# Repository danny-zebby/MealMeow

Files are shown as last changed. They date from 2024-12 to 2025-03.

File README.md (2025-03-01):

# MealMeow

## General Description
The general concept of this design seeks to solve the problem of caring for your cats or dogs while you are away for an extended period of time. Our aim is to create a product that can handle the feeding and hydrating of several pets while the owner is away. We will create a device that will dispense water, and food to pets at amounts configurable by the owner at regular intervals and it will do so independently. Our product will only require the attention of the owner when any of the aforementioned items is depleted. When food has run low, or when any of the dispensable items have run out, our device will alert the owner using sound alerts and a warning indicator light.

## Behavioral Specification
### Food Storage and Dispensation
Food will be stored in a container and will be dispensed using a rotating paddle at the bottom of the container. We intend to control this rotating paddle using a direct-current stepper motor. The food container will be equipped with a IR distance sensor placed at one side of the container, once the IR distance sensor measures the other side of the container, it will be known that there is no food at that level. This will cause the unit to light an LED as a low food level indicator for the user. As an alternative, another sensor can be reading the distance between the sensor and what’s in front. 
Once the food level sensor measures that the container is low on food, our product will notify the user of low food levels. A flashing LED will turn on when a sensor has indicated low levels, the LED will be color coordinated depending on the container. We aim for our product to use a speaker to alert the user with either a tone or voice.

### Water Storage and Dispensation
Our device will store water in a large water bladder connected to a motorized water solenoid valve, which will control the flow of water from the reservoir and through tubing ending in the pet’s water bowl.

### Food and Water Measuring
Our product will be equipped with pressure sensors below the surface where the food and water bowls are placed. We intend to use either digital load cell weight sensors or strain gauges to sense the weight placed on the food and water bowls. The unit will calculate the amount of food or water that has been dispensed by calculating the difference in pressure at the food and water bowls.

### User Interface
User interface will consist of 3 buttons and a 20x2 LCD screen. The unit will have 2 “modes” which will allow the user to program the unit. When the “food” mode is engaged, the screen will display the amount of food that is to be dispensed daily. From this mode, the user can use two of the buttons to increment and decrement the amount of food to be dispensed in increments of 10g. This will allow the user to relatively precisely control the amount of food the pet receives each day in order to ensure the pet remains at a healthy weight. 

## Subsystem Control
### Water Dispenser
Components: 
Plastic Water Solenoid Valve - 12V - 1/2" Nominal (adafruit 997)
Darlington Transistor TIP-120

Description:
Plastic valve with solenoid that is activated with power.Solenoids activates when current is passed Max voltage is 12 V. It is one way flow and is suggested to use a TIP 120 to drive from a MCU. The amount of time active or water being dispensed will be determined by trial and error.

### Food Dispenser Control
Component Name: Small Reduction Stepper Motor 12V 
Adafruit Product ID 918

Description
	This stepper motor works on DC power. We chose this motor to operate the food dispenser mechanism because stepper motors like this one are geared to move at approximately rotation “steps”, which will allow us to more accurately control flow of food into the pet’s food bowl, which is an important part of our design. This particular stepper motor has 516 steps. This type of motor also holds its position strongly, which is important for the dispersal mechanism so that the mechanism does not rotate under the weight of the pet’s food. This type of motor is controlled by sending electrical pulses which instruct the motor to turn one step. A motor driving circuit is necessary to operate this motor. 

### Food Storage Level Sensor Control
Component Name: Infrared Proximity Sensor - Sharp GP2Y0A21YK

Paragraph description:
This infrared proximity sensor will be placed at a low enough in the container to sense when the food is near empty, but also high enough for the pet to have one or two more bowls. As long as the product is on the infrared sensor is also on. The infrared sensor is emitting an infrared light that bounces back into the built infrared sensor. After doing some math for how long it took the sensor to submit and receive the light, it calculates the distance of what’s in front of it. If the distance measure is the diameter of the container, then it is known there’s no food across the sensor, marking the container low. If the sensor measures anything less than the diameter then it will be known that the container has enough food before refilling.
	An infrared sensor was selected because it was better at reading non flat surfaces, which is perfect for pet food. According to the datasheet, the sensor has trouble being accurate for low levels. Which is not a concern for our purposes since we do not need to know the exact distance from the sensor to the, we just need to know the distance from the sensor to the container. My understanding of the infrared proximity sensor coding is that it sorts 25 samples of analogread, then it takes the median from those samples. Then maps it 0 to 5000, divides by 5000, takes that to the power of -1.2045 and finally multiplies to 27.728. This equation gives us the conversion from Voltage to centimeters.

### Water Reservoir Level Sensor Control / Standard Level Sensor(alternative) 
Component Name: SEN0509 - Capacitive pipeline liquid level sensor
			PLS-051B-3PPI-Standard Level Sensor (in case other sensor fails)

Description: 
	Meant for non-metallic pipes, made with plastic, and signals low when water is present. It’s range is from 2.5 - 5.5V. Can be used to detect the level of water either high or low water level. Signal will go directly to a general purpose I/O connection on a MCU.Sensor is going to placed near the bottom of the tank, connected with two line tubes 6mm of diameter. The tube will be connected to the tank from the bottom and the other end will be attached to the top of the tank, capped off to prevent spillage.

Alternatively, the standard level sensor can be used just in case the other sensor stops working. This sensor will receive power and pass through and once the water level reaches a low state them.The relay will switch to no power pass through. For this component, it has a large capability to handle 200V at 1 A.Hence, it will operate at 5.5V for convenience that other water sensor component max is at 5.5V.

### Food Scale Sensor Control
Component Name: Strain Gauge + HX711

Description:
The MealMeow uses two strain gauges attached to two boards for where the pet’s bowl to be placed on. The project uses user input, via the LED screen, to determine how much of a serving of food and water the bowls should have. Once the MealMeow is ready to dispense either the food or water, it will measure the current weight of the board and bowl, then will dispense until it reaches the desired amount of grams. 
For our purposes the usage of the Strain Gauge is simple, however implementation of the HX711 proves difficult. We are considering alternative methods for this chip. The main usage of the chip is a 64 or 128 gain followed by a 24 bit Analog-to-Digital Converter (ADC). The HX711 has an input MUX and a digital interface that uses the clock to read the 24 bits. The HX711 datasheet has transistors parts, capacitors and resistors with the build for the purposes for using the strain gauges we plan on using.

## Power Supply
Components:
Switching Regulator, LTC3601 from Linear Technology
AC/DC Wall Adapter, Tensility International Corp 16-00031

This project will utilize two voltage regions on the PCB, at 12V and at 5V. The processor and most peripherals will utilize the 5V region, and the water and food dispensal motors will operate using the 12V region. In order to supply power to the PCB, we will use an AC to DC wall adapter from. This wall adapter will supply our board with 12 volts of DC power. We then intend to use a switching regulator to construct a step-down circuit which will output 5V of power.
Microprocessor: 
ATMEGA4808-XF

Description: 
The Microprocessor we decided to use for our project is the ATMEGA4808-XF. This microprocessor is an 8-bits fits our needs as it provides adequate speed, memory, and ports our project needs. The MealMeow’s functionality does not not rely on speed, so the 20MHz this chip provides is plenty for our purpose. This chip also has various connectivity ports, including I^2C. We plan on using I2C as our peripherals and interfaces do not all need to be working all at once. The ATMEGA4808-XF was ultimately chosen over other similar chips due to the expansion in flash memory, sufficient number of ports, and price. We have the flexibility of adding features if necessary, storing text and storing audio.

Attributes:
Voltage: 1.8V ~ 5.5V
Temperature: -40℃ ~ 125℃
Core Size: 8-Bit
Speed: 20MHz
Clock Cycle: Max 20MHz at 4.5V ~ 5.5V
Flash Memory Size: 48KB
Peripherals: 3x UART, 1x SPI, 1x I2C

## Speaker Output Control
Component Name: SPEAKER 8OHM 2W TOP PORT 84DB - 
2223-CMS-402811-28SP-ND
Description:
This general purpose speaker has a frequency range between 300 Hz and 20 kHz. The main focus of this speaker was so that you will be able to hear it from a fairly large amount of distance between you and the speaker. This will be connected to the straight from the processor since we do not intend to project sound at a high volume.

## LCD screen
Component Name: LED Character Display.  
LCD MOD 40DIG 20X2 TRANSFLCT WHT - NHD-C0220BIZ-FSW-FBW-3V3M-ND

Description: 
This LED - yellow/green character display will have 2 lines x 20 characters and its character format is 5 x 8 dots. The interface that I will be using is I2C. Since I will be using I2C there will only be two pins I will be using. This also has a built-in DC supply for VLCD. The only thing that this display needs to get connected to is the processor since it already has power.

## Software
### Processor (Software) ATMEGA4808-XF:
Booting Modes: (Page 465 of Datasheet)
Programing: To program our chip, we will be using a hardware programer: Pocket AVR Programmer . Using the software Arduino Bootlander, the chip should be able to boot into an operabl;e state. Bootloader is the software used in Arduinos when you press the reset and ON button. This microprocessor should be compatible with Bootlander as it is part of the ATMEGA Arduino family. 

## Conclusion
As a group, we had a clear purpose, to make the best cat feeder we could make. One of the components of our senior project that as a group we had decided was of priority to all of us was to ensure our project had a purpose. The MealMeow archives this by ensuring Christians cats will have the best dining experience we can make. All of the components and features of the MealMeow have taken into consideration the sensibilities and comfort of a cat. When the project was in its early stages, the task seemed quite intimidating. Now that we are in this stage and have our features and components selected, we are excited to see the MealMeow in action soon. We expect troubles and difficulties ahead, but are excited to confront these challenges.

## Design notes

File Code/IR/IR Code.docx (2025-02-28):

//#define IR_SAMPLE 25

//#define PINIR A0 // PA3

//#define PINLED 9 // PD3

void setup() {

pinMode (A0, INPUT);

analogReference(DEFAULT);

Serial.begin(9600);

}

void loop() {

int distanceCM, median, LEDistance;

float current;

int ir_val[25] = {};

// Gather samples

for (int i=0; i<25; i++){

ir_val[i] = analogRead(A0);

}

// Sort Samples

for(int i=0; i<(25-1); i++) {

bool flag = true;

for(int o=0; o<(25-(i+1)); o++) {

if(ir_val[o] > ir_val[o+1]) {

int t = ir_val[o];

ir_val[o] = ir_val[o+1];

ir_val[o+1] = t;

flag = false;

}

}

if (flag) break;

}

// get mid value

median = ir_val[25/2];

// disctance calculations

distanceCM = 29.988 * pow(map(median, 0, 1023, 0, 5000)/1000.0, -1.173);

LEDistance = (distanceCM*255/73) -24;

analogWrite(9, LEDistance);

// // Print the measured distance to the serial monitor:

// Serial.print("Mean distance: ");

// Serial.print(distanceCM);

// Serial.println(" cm");

delay(1000);

}

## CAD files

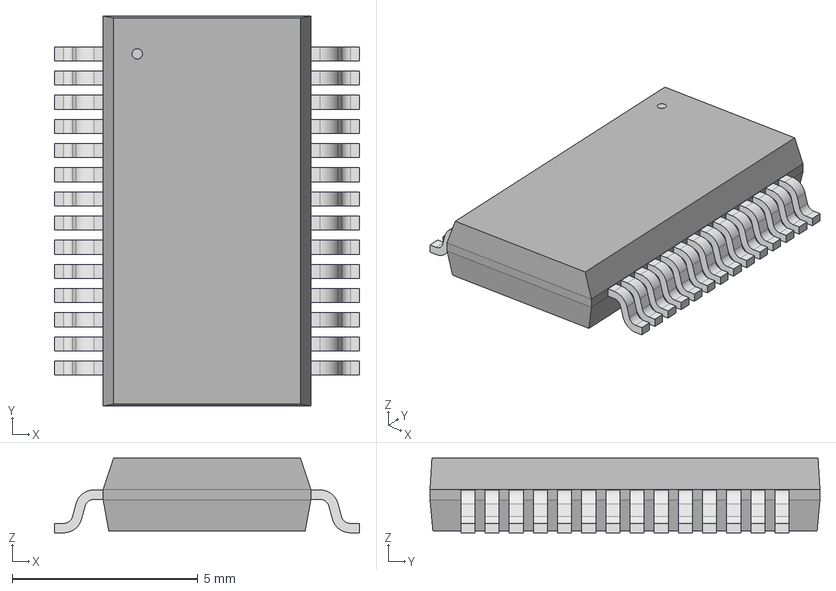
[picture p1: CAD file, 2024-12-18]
Circuit Schematics/Component Schematics (Downloaded from Manufacturer)/SSOP28_SS_MCH.step
8.20 x 10.5 x 2.01 mm

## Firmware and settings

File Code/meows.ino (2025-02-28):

string prompt [3] = {"Amount of per Day"," ","are you sure"};
bool lowWater = false;// for pouring
bool lowFood = false;
bool isZero = false;
long startSystem = millis();// first time 
long currentTime = 0; //time of measure
long setTime = 0; // interval to wait
int grams = 0;

int maxValue = NULL;// needs to up date************!!!!!

bool needsReset = false;
int mL = 4000;// 4s for x ml when dispensing liquid
////Four sides

//PINOUT//UPPER--pins(32-24)
pinMode(PA2,OUTPUT);//SOLENOID
PinMode(PA1,INPUT_PULLUP);//Button1
//pinMode(PF6,INPUT);//Reset

//RightMost--pins(22,25,24)
pinMode(PF2,INPUT_PULLUP);//Button2
pinMode(PF5,OUTPUT);//LCD 1(..)
pinMode(PF4,OUTPUT);//LCD 2(..)

//LOWER--pin(13-7)
pinMode(PD3,INPUT);//WaterSensor
pinMode(PD2,INPUT_PULLUP);//Button3
pinMode(PD1,OUTPUT);//Speaker
//Motor Pins
pinMode(PD0,OUTPUT);//1
PinMode(PC3,OUTPUT);//2

//LeftMost--Pin(8-1)
pinMode(PC2,OUTPUT);//3
pinMode(PC1,OUTPUT);//4

pinMode(PC0,OUTPUT);// en
pinMode(PA7,OUTPUT);//motor reset
pinMode(PA6,??)://FAULT

//SCALE
pinMode(PA5,??);//SCK 
pinMode(PA4,??);//DAT

pinMode(PA3,INPUT);//FoodSensor /// look how it works with interrupts

/////******MENU******/////
//// Interrupts global

volatile int center = 0;

volatile bool confirm = 0;

volatile bool emptyBox = false;

attachInterrupt(digitalPinToTnterrupt(PA1),upOne,CHANGE);
attachInterrupt(digitalPinToTnterrupt(PA1),downOne,CHANGE);
attachInterrupt(digitalPinToTnterrupt(PA1),select,CHANGE);

attachInterrupt(digitalPinToTnterrupt(PD3),empty,LOW);// switch goes low interrupt activates

////IRS////

void upOne(){ /// for menu
    center++;
}
void downOne(){
    center--;
}
void select(){
    confirm =!confirm;
}
void empty(){ /// no food or water
    needsReset = !needsReset;
}


////****LED****////
void display1(){
  while(confirm){
    lcd.setCursor(1, 0);
    lcd.print("    MealMeow    ");
    lcd.setCursor(1, 1);
    lcd.print("Hit sel to cont.");
    delay(3000);
    lcd.clear();
  
    lcd.setCursor(2, 0);
    lcd.print("   Hungry? ");
    lcd.setCursor(2, 1);
    lcd.print("   Thirsty?");
    delay(3000);
    lcd.clear();
  }
}
void display2(){
  while(confirm){
    int grams = grams + center;
    if(grams < 0){
        grams = 0;
      }
    center = 0; 
    lcd.setCursor(0, 0);
    lcd.print("How many grams");
    lcd.setCursor(0, 1);
    lcd.print("to dispense:");
    lcd.print(val2);
    lcd.print("g");
    delay(3000);
    lcd.clear();
  }
}

////*****Speaker****/////

void playSound(){
  tone(PD1,784,4000);
}

////***Zero Scale***////
void  zero(){
    //stub
  }

///Motors///
void motor(){
  //stub
}
/// solenoid///
void solenoid(){
  digitalWrite(PA2,HIGH);
  delay(mL);
  digitalWrite(PA2,LOW);
}

////***Looping Process***////

  void weigh(){
    //stub
  }
  void pour(String val){
    if(val=="water"){
      solenoid();
    }
    if(val=="food"){
      motor();
    }
  }


//.....goes in loop()
while(needsReset){
  noInterrupts();
  playSound();
  int button = digitalRead(PA1);
  if (button == HIGH){
    needsReset = !needsReset;
    interrupts();
  }
}
  if(isZero){
    weigh();
  }
if (!maxValue){
  if(lowWater){
    pour("water");
  }
  if(lowFood){
    pour("food");
  }
}


// void setup() {
//   // put your setup code here, to run once:
display1();
confirm =!confirm();
display2();
confirm =!confirm();

// }

// void loop() {
//   // put your main code here, to run repeatedly:

// 
  

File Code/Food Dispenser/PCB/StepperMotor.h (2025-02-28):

//Number of steps in the motor for one rotation
#define STEPS 516 //2038

//Stepper Driver Pins
#define RESET  PIN_PA7    //5 Reset Pin, active high to reset
#define ENABLE PIN_PC0    //6 Enable pin, active low to enable
#define FAULT  PIN_PA6    //4 Fault pin, stepper driver outputs a 1 if there is some issue

/*
//Motor to board connections

Blue == P2B == PIN_PC1 == bottom input on board
Pink == P2A == PIN_PC2


Red == VDD

Yellow == P1B == PIN_PC3
Orange == P1A == PIN_PD0

*/

#define P1A PIN_PD0
#define P1B PIN_PC3
#define P2A PIN_PC2
#define P2B PIN_PC1

#define stepperDelayMicroSeconds = 100;



void StepOnceBackward(){
  delay(stepperDelayMicroSeconds);
  //STEP 1
  digitalWrite(P1A, LOW);
  digitalWrite(P1B, HIGH);
  digitalWrite(P2A, HIGH);
  digitalWrite(P2B, HIGH);
  delay(stepperDelayMicroSeconds);
  //STEP 2
  digitalWrite(P1A, HIGH);
  digitalWrite(P1B, LOW);
  digitalWrite(P2A, HIGH);
  digitalWrite(P2B, HIGH);
  delay(stepperDelayMicroSeconds);
  //STEP 3
  digitalWrite(P1A, HIGH);
  digitalWrite(P1B, HIGH);
  digitalWrite(P2A, LOW);
  digitalWrite(P2B, HIGH);
  delay(stepperDelayMicroSeconds);
  //STEP 4
  digitalWrite(P1A, HIGH);
  digitalWrite(P1B, HIGH);
  digitalWrite(P2A, HIGH);
  digitalWrite(P2B, LOW);
  delay(stepperDelayMicroSeconds);  
}

void StepOnceForward(){
  delay(stepperDelayMicroSeconds);
  //STEP 4
  digitalWrite(P1A, HIGH);
  digitalWrite(P1B, HIGH);
  digitalWrite(P2A, HIGH);
  digitalWrite(P2B, LOW);
  delay(stepperDelayMicroSeconds);
  
  //STEP 3
  digitalWrite(P1A, HIGH);
  digitalWrite(P1B, HIGH);
  digitalWrite(P2A, LOW);
  digitalWrite(P2B, HIGH);
  delay(stepperDelayMicroSeconds);

  //STEP 2
  digitalWrite(P1A, HIGH);
  digitalWrite(P1B, LOW);
  digitalWrite(P2A, HIGH);
  digitalWrite(P2B, HIGH);
  delay(stepperDelayMicroSeconds);
  
  //STEP 1
  digitalWrite(P1A, LOW);
  digitalWrite(P1B, HIGH);
  digitalWrite(P2A, HIGH);
  digitalWrite(P2B, HIGH);
  delay(stepperDelayMicroSeconds);  
}

void StepperSetup() {
  pinMode(RESET, OUTPUT); //Reset Pin, active high to reset
  digitalWrite(RESET,LOW);
  
  pinMode(ENABLE, OUTPUT);  //Enable pin, active low to enable
  digitalWrite(ENABLE, LOW);

  pinMode(FAULT, INPUT);

  pinMode(P1A, OUTPUT);
  pinMode(P1B, OUTPUT);
  pinMode(P2A, OUTPUT);
  pinMode(P2B, OUTPUT);
}

void DispenseFood() {
  for (int i = 0; i < 8; i++){
    StepOnceForward();
  }
  for (int i = 0; i < 4; i++){
    StepOnceBackward();    
  }
}
